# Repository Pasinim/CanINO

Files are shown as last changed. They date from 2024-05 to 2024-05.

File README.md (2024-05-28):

# CanINO
Progetto realizzato per il corso di [sistemi embedded](https://gitlab.di.unimi.it/sistemiembedded/2022-2023).
## Introduzione

Il progetto `CanINO` è un dosatore automatico per animali, progettato per fornire cibo agli animali domestici in modo automatico, seguendo quantità e orari prestabiliti.

## Sensori ed attuatori utilizzati

| Sensore/Attuatore | Funzione |
| --- | --- |
| Arduino | Microcontrollore |
| Potenziometro | Permette il controllo dell'orario di erogazione e della quantità di cibo erogabile (in modalità setup) |
| Display OLED I2C  | Permette la visualizzazione dell'orario corrente, dell'orario di erogazione e della quantità dì cibo che verrà erogata. |
| 28BYJ-48 | Stepper motor che permette l'erogazione del cibo |
| ULN2003 | Driver per il controllo dello stepper motor |
| Cella di carico | Produce un segnale di uscita in base alla deformazione a cui è soggetto, viene utilizzato per pesare il cibo erogato |
| HX711 | Convertirore analogico-digitale che converte l'output della cella di carico in grammi |
| DS3231 | RTC che mantiene l'orario impostato in assenza di alimentazione alla board |
| Pulsante | Utilizzato per cambiare tra la modalità di configurazione tra orario e quantità di cibo e viceversa |
| Switch | Utilizzato per entrare in modalità setup |

## Funzionalità

Le funzionalità offerte sono le seguenti.

1. Dosaggio del cibo: il dosatore può erogare una quantità specifica di cibo, regolata tramite il potenziometro,
2. Programmazione dell'orario: è possibile impostare l'ora in cui erogare il cibo. Il dosatore erogherà automaticamente il cibo alla stessa ora ogni giorno,
3. Display delle Informazioni: il display OLED permette di visualizzare la quantità di cibo (g) impostata e l'orario dell'erogazione,
4. Misurazione del peso: la cella di carico misura il peso del cibo, disattivando l'erogatore quando la quantità erogata corrisponde a quella impostata.
5. Mantenimento dell'ora corretta (dopo averla impostata correttamente la prima volta) anche in seguito allo spegnimento della board, grazie al modulo DS3231 che è alimentato da una pila.

## Macchina a stati finiti

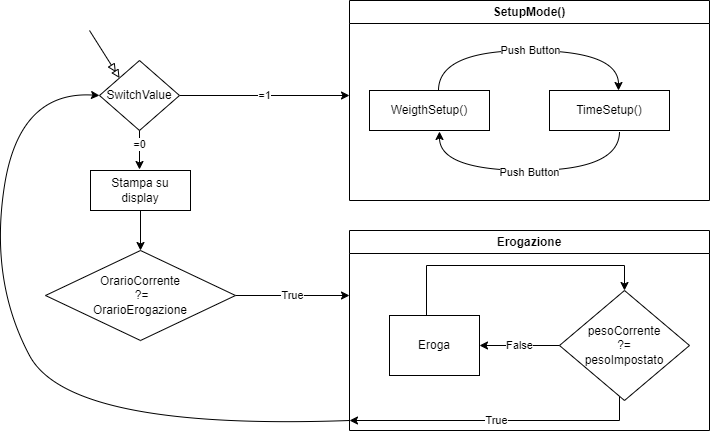
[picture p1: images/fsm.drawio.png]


## Funzionamento

Il progetto "CanINO" funziona nel seguente modo:

1. L'utente sceglie se avviare la modalità "Setup" o "Idle" tramite un interruttore;

2. _Modalità Setup_:
   
   - Il pulsante permette di passare dalla regolazione dell'orario alla regolazione della quantità di cibo da erogare e viceversa
   
   - La quantità di cibo e l'orario di ergoazione sono impostabili tramite il potenziomentro
   
   - La quantità di cibo erogabile va da un limite inferiore definita nel codice tramite la costante `lower` mentre quella massima è definita dalla costante `upper`.

3. _Modalità Idle_:
   
   -  Quando arriva l'ora impostata, il motore del dosatore si attiva per erogare la quantità di cibo impostata;

   -  La cella di carico misura il peso del cibo nel contenitore e disattiva il motore dell'erogatore al raggiungimento del peso.

## Schema dei Collegamenti

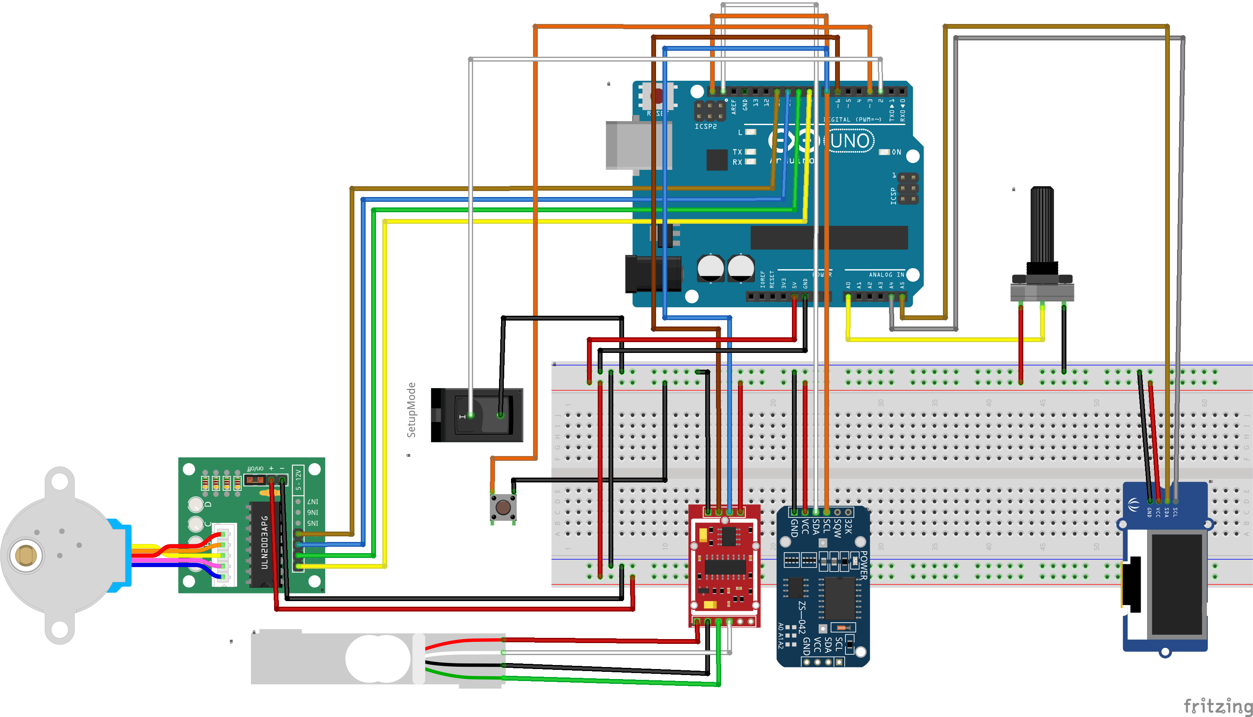
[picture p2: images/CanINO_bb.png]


---

## Problemi riscontrati

- Uno dei principali problemi incontrati riguarda il processo di erogazione del cibo. Inizialmente, il progetto prevedeva l'utilizzo di un imbuto sigillato con un pezzo di ferro, mentre l'erogazione era regolata tramite dei servo motori collegati con degli elastici all'imbuto erogatore e al pezzo di metallo. Per erogare il cibo, era necessario azionare i servo motori per aprire il pezzo di metallo come una sorta di botola.

Con questa implementazione però non era possibile controllare con precisione il cibo erogato quindi ho stampato un dosatore in 3D che permette l'erogazione in modo più uniforme e preciso. Anche in questo modo però ho riscontrato dei problemi, infatti sia con del riso sia con delle crocchette per cani il cibo si incastrava nel dosatore fermando il motore. Per questo motivo ho utilizzato delle sfere di metallo. Ovviamente non si tratta di una soluzione ideale, soprattutto perchè le sfere si incastrano comunque nel cilindo superiore dell'erogatore. Per ovviare a questi problemi bisognerebbe modellare l'erogatore in un altro modo.

- Durante l'erogazione del cibo l'orario visualizzato sul display non viene aggiornato ma rimane fermo (al secondo precedente) all'orario di erogazione. Si tratta di un problema di poco conto, anche se bisogna considerare che l'erogazione del cibo non avviene in modo rapido, impiegado anche minuti se la quantità di cibo è elevata. Per risolvere questo problema si potrebbe ricorrere ad un motore con voltaggio superiore per eseguire più rotazioni al minuto oppure aggiornando la funzione di erogazione inserendo al suo interno il refresh del display.

---

## Codice rilevante

#### Impostazione dell'orario corrente

Il modulo RS3231 permette il mantenimento dell'orario anche se la board non è alimentata. Tuttavia è necessaria la configurazione se il modulo non è in esecuzione e ciò viene fatto con il seguente codice.

```c
  if (! rtc.isrunning()) {
    rtc.adjust(DateTime(F(__DATE__), F(__TIME__)));
  }
```

#### Calibrazione cella di carico

Il HX711 è un convertitore analogico-digitale (ADC) con una risoluzione fissa di 24 bit e prima di utilizzarla per misurare il peso è necessario effettuare una calibrazione per ottenere letture accurate e coerenti dalla cella di carico collegata.

La calibrazione è stata eseguita con il seguente [codice ]
(https://github.com/RobTillaart/HX711), i valori ottenuti sono stati salvati nelle variabili `offset_hx711` e `calibration_factor`.

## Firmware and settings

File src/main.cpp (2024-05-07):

// Librerie per il display
#include <Wire.h>
#include <Adafruit_GFX.h>
#include <Adafruit_SSD1306.h>
#include <Arduino.h>
#include <HX711.h>
#include <RTClib.h>
#include <Stepper.h>
// #include <Servo.h>

/** */  
#define SCREEN_WIDTH 128
#define SCREEN_HEIGHT 64

// Creo un oggetto display. Vengono impostate le grandezze del display,
//  viene inizializzata la libreria per comunicare tramite il bus I2C
Adafruit_SSD1306 display(SCREEN_WIDTH, SCREEN_HEIGHT, &Wire, -1);

// Step necessari per effettuare una rotazione completa del motore
const int stepsPerRevolution = 2048;
/** I pin del motore devono essere collegati rispettivamente ai pin IN1-IN3-IN2-IN4 */
Stepper myStepper = Stepper(stepsPerRevolution, 8, 10, 9, 11);

/** Inizializzazione dei pin */
const int potPin = A0; 
const int switchPin = 2;
const int buttonPin = 3;
const int data_loadCell = 6;
const int clock_loadCell = 7;

/** Range quantita di cibo erogabile, rispettivamente minimo e massimo */
const int lower = 50;
const int upper = 200;


/** Definizione delle variabili */
int orario[2]; /** orario nel formato hh:mm */
int quantita = lower; /** quantita di cibo da erogare [g] */ 
const int intervallo = 5; /** Passo con cui viene incrementato/decrementato l'orario (in minuti) */

int buttonValue = 0;      /** Segnale del pulsante */  
int lastButtonValue = 0; /** Ultimo segnale letto del pulsante*/  
int buttonPushCounter = 0;   /** Contatore che tiene traccia del numero di pressioni del tasto*/   


float calibration_factor = 1984.322021; /** Valore di calibrazione per la cella di carico*/ 
float offset_hx711 = 2321710; /** Offset della cella di carico */ 
HX711 scale; /** Variabile di istanza per utilizzare il modulo HX711*/


RTC_DS1307 rtc;  /** Variabile di istanza per utilizzare il modulo rtc*/



void setup() {                                          
  Serial.begin(9600); // Inizializza la comunicazione seriale a 9600 bps
  Wire.begin();
  display.begin(SSD1306_SWITCHCAPVCC, 0x3C); // L'indirizzo I2C del display potrebbe essere diverso (0x3C è l'indirizzo più comune)
  display.clearDisplay();
  display.setTextSize(1);
  display.setTextColor(SSD1306_WHITE);

  pinMode(switchPin, INPUT_PULLUP);
  pinMode(buttonPin, INPUT_PULLUP);
  scale.begin(data_loadCell, clock_loadCell);
  scale.set_offset(offset_hx711); 
  scale.set_scale(calibration_factor);
  /** Imposta la tara*/
  scale.tare();

  if (! rtc.begin()) {
    Serial.println("Couldn't find RTC");
    Serial.flush();
    while (1) delay(10);
  }
  if (! rtc.isrunning()) {
    rtc.adjust(DateTime(F(__DATE__), F(__TIME__)));
  }
}

/** Restituisce l'offset necessario per centrare la stringa sulle x del display OLED */
int centerDisplay(char s[]){
  return (SCREEN_WIDTH - strlen(s) * 6) / 2;
}

/** Permette di impostare l'orario in cui erogare il cibo tramite il potenziometro.
 Il passo dell'orario è definito dalla variabile `intervallo` (in minuti). 
 */
void timeSetup(){
  Serial.println("Time setup");
  int valorePotenziometro = analogRead(potPin);
  int timeValue = map(valorePotenziometro, 0, 1023, 0, 60/intervallo*24); 
  orario[0] = timeValue / (60/intervallo);
  orario[1] = (timeValue % (60/intervallo)) * intervallo;

/** Stampa su display **/
  char str[50]; 
  strcpy(str, "SETUP");
  display.setCursor(centerDisplay(str), 0);
  display.println(str);
  strcpy(str, "ORARIO");
  display.setCursor(centerDisplay(str), 8);
  display.println(str);
  strcpy(str, "Imposta l'orario di \nerogazione: ");
  display.setCursor(centerDisplay(str), 18);
  display.print(str);
  sprintf(str, "%02d:%02d", orario[0], orario[1]);
  display.println(str);

  /** Definisco la variabile orarioErogazione: yyyy/mm/gg, orario[0]:orario[1]:00;  **/
  DateTime orarioErogazione(rtc.now().year(), rtc.now().month(), rtc.now().day(), orario[0], orario[1], 0);
  display.display();
}


/** Permette di impostare la quantità (g) di peso da erogare tramite il potenziometro.
 Il range di valori che assume va da `lower` a `upper`. 
 */
void weightSetup(){
  Serial.println("weight setup");
  int valorePotenziometro = analogRead(potPin);
  quantita = map(valorePotenziometro, 0, 1023, lower, upper);

/** Stampa su display **/
  char str[50]; 
  strcpy(str, "SETUP");
  display.setCursor(centerDisplay(str), 0);
  display.println(str);
  strcpy(str, "QUANTITA'");
  display.setCursor(centerDisplay(str), 8);
  display.println(str);
  strcpy(str, "Imposta la quantita\n di cibo: ");
  display.setCursor(centerDisplay(str), 18);
  display.print(str);
  sprintf(str, "%d", quantita);
  display.println(str);
  display.display();
}

/**
  Modalità che permette di modificare la quantità di cibo da erogare
  e l'orario in cui viene erogato.
  Premendo il pulsante è possibile alternare tra l'impostazione dell'orario e del peso.
*/
void setupMode(){
  buttonValue = digitalRead(buttonPin);
  if (buttonValue != lastButtonValue) {
    if (buttonValue == HIGH) {
      buttonPushCounter++;
    } 
    delay(50);
  }
  lastButtonValue = buttonValue;
  if (buttonPushCounter%2==0)
    timeSetup();
  else
    weightSetup();
}

/**
* Restiutuisce true se l'orario impostato corrisponde all'orario attuale
**/
bool checkTime(){ //da togliere e da confrontare con int orario[]
  DateTime time = rtc.now();
  // Serial.println(time.timestamp(DateTime::TIMESTAMP_TIME));
  // if (time.hour() == o[0] && time.minute() == o[1]) 
  if (time.hour() == orario[0] && time.minute() == orario[1]) 
    return true;
  return false;
}

/**
 * Eroga il cibo fino a quando non si raggiunge la quantità impostata.
 * Il motore esegue un giro completo in senso orario, poi metà giro in senso orario.
 * Questo viene eseguito per evitare che il cibo rimanga incastrato nel tubo di erogazione.
 * 
 */
void eroga(){
  // Serial.println("\t Eroga");
  while (scale.get_units(1) < quantita){
    Serial.print("peso attuale:"); 
    Serial.println(scale.get_units(1));
   	myStepper.setSpeed(15);
	  myStepper.step(stepsPerRevolution);
    myStepper.setSpeed(15);
	  myStepper.step(-stepsPerRevolution/3);
    delay(100);
  }
  // Aggiungendo questo print non funziona nulla??
  // Serial.println("\tErogazione completata");
  return;
}

/**
 * Stampa sul display l'orario attuale e la quantità di cibo erogata.
 * @param currentTime orario corrente
 */
void printInfo(DateTime currentTime){
    char buffer[50];
/** Conversione dell'orario in stringhe*/
    char hourStr[3];
    char minuteStr[3];
    char secondStr[3];
    itoa(currentTime.hour(), hourStr, 10);
    itoa(currentTime.minute(), minuteStr, 10);
    itoa(currentTime.second(), secondStr, 10);

  /** Costruzione e stampa della stringa dell'orario */
    strcpy(buffer, " ");
    strcat(buffer, hourStr);
    strcat(buffer, ":");
    strcat(buffer, minuteStr);
    strcat(buffer, ":");
    strcat(buffer, secondStr);
    strcat(buffer, "\n");
    display.setCursor(centerDisplay(buffer), 4);
    display.println(buffer);

    /** Stampa la quantità di cibo erogta all'orario impostato*/
    strcpy(buffer, "Verranno erogati ");
    display.setCursor(centerDisplay(buffer), 18);
    display.println(buffer);
    itoa(quantita, buffer, 10);
    strcat(buffer, "g");
    display.setCursor(centerDisplay(buffer), 24);
    display.println(buffer);
    strcpy(buffer, " di cibo alle ");
    strcat(buffer, itoa(orario[0], hourStr, 10));
    strcat(buffer, ":");
    strcat(buffer, itoa(orario[1], minuteStr, 10));
    display.setCursor(centerDisplay(buffer), 32);
    display.println(buffer);

    display.display();
}

/**
 * Metodo di debug per stampare sul monitor seriale le variabili di stato.
 */
void debug() {
  Serial.println("********** DEBUG **********");
  Serial.print("orario: ");
  Serial.print(orario[0]);
  Serial.print(":");
  Serial.println(orario[1]);
  Serial.print("quantita: ");
  Serial.println(quantita);
  Serial.print("buttonPushCounter: ");
  Serial.println(buttonPushCounter);
Serial.print("ButtonValue: ");
  Serial.println(buttonValue);
  Serial.print("switchValue: ");
  Serial.println(digitalRead(switchPin));
  Serial.print("scale.get_units(1): ");
  Serial.println(scale.get_units(1));
  Serial.println("***************************");
  delay(500);
}

void loop() { 
  // debug();
   DateTime currentTime = rtc.now();
   display.clearDisplay();
   display.setCursor(0, 0);
  int switchValue = digitalRead(switchPin);
  if (switchValue == HIGH) setupMode();
  else
    printInfo(currentTime);
  if (checkTime())
    eroga();
  
}

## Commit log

2023-08-01 Aggiunto schema fritzing
    [CanINO.fzz]
2023-08-07 Fix potenziometro
    [CanINO.fzz]
2023-08-09 Aggiunto switch per setupMode
2023-08-09 Aggiornato schema
    [CanINO.fzz]
2023-08-20 Aggiunto metodo di debug
2023-08-21 Aggiunto sketch calibrazione cella di carico
2023-08-21 Aggiunto hx711
    [CanINO.fzz]
2023-08-22 Aggiunto sketch di test per clock
2023-09-01 Test sensori
2023-09-27 Fix oled print
2023-10-11 Fix print su display in setupTime e setupWeight
2023-10-18 Aggiunti servo
    [CanINO.fzz]
2023-10-18 Modificate variabili per stampa su oled
    [CanINO.fzz]
2023-10-20 Cancellati sketch ArduinoIDE
2023-10-22 Fix print in setup
    [main.cpp]
2023-10-22 fix print fuori da setup
    [main.cpp]
2024-05-06 Rimossi servo
2024-05-06 Aggiunto servo motor
    [CanINO.fzz]
2024-05-06 Aggiunto motore
    [CanINO.fzz]
2024-05-06 Fix crash quando stampa su display
    [main.cpp]
2024-05-07 Modificato intervallo di cibo erogabile per renderlo funzionante con il prototipo
